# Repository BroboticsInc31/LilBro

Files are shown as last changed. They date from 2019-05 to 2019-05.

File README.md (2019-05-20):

# LilBro by Brobotics Inc. 

Lil'Bro is a 3D printed, open source quadrupedal robot which allows researchers to investigate agile gait locomotion and may duplicate, modify, and create new methods for the robot. 

Related Videos: </br>
Calibration - https://youtu.be/Aq8ONlaq-m4 </br>
Startup routine - https://youtu.be/N4R1693wzeQ </br>
Charging Batteries - https://youtu.be/PBRBTcRp_1k </br>
Using the power supply - https://youtu.be/rCxc9LMYpuw </br>

Install Dependencies: </br>
ODrive - https://docs.odriverobotics.com/ </br>
Numpy - https://www.numpy.org/</br></br>

Download the repository.</br>
in directory (where repository was downloaded) run:</br>
   ```
   sudo python3 main.py 
   ```
   </br>
   
</br></br>

broboticsinc

LilBro

Lil'Bro V1.0

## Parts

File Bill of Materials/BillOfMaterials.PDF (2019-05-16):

*NOTE:
- PRICES MAY VARY UPON CURRENT MARKET VALUE
- SHIPPINGNOT INCLUIDED; SHIPPING COST MAY VARY BASED ON DELIVERY LOCATION
APPROVAL DATE: | 1-29-2019
PART COUNT: | 512
TOTAL COST: | $2,187.77

Brobotics Inc. Purchased Bill of Materials
ITEM NO. | QTY. | PART NUMBER | DESCRIPTION | MATERIAL | VENDOR/NOTES | PRICE
1 | 12 | 509 | FASTENER, LEG MOUNT | PURCHASE | 93897A542 MCMASTER-CARR | $8.45 /25
2 | 12 | 510 | WASHER, LOCK | PURCHASE | 3573A16 MCMASTER-CARR | $8.21 /100
3 | 24 | 511 | NUT, HEX | PURCHASE | 96557A109 MCMASTER-CARR | $8.63 /50
4 | 4 | 512 | FASTENER, COVER | PURCHASE | 96817A274 MCMASTER-CARR | $6.69 /25
5 | 8 | 513 | MOTOR, DC | PURCHASE | D5065-270KV, ODRIVE | $69.00 EA
6 | 8 | 514 | ENCODER, CPR | PURCHASE | CVI AMT102-V, ODRIVE | $39.00 EA
7 | 16 | 515 | FASTENER, ENCODER | PURCHASE | 90666A104, MCMASTER-CARR | $8.40 /100
8 | 28 | 516 | HOLDER, CABLE | PURCHASE | 7565K31, MCMASTER-CARR | $5.74 /25
9 | 32 | 517 | FASTENER, MOTOR | PURCHASE | 93705A824, MCMASTER-CARR | $7.25 / 25
10 | 48 | 518 | FASTENER, MOTOR HOUSING | PURCHASE | 91292A114, MCMASTER-CARR | $4.72 /100
11 | 12 | 519 | LOCKNUT, LEG-JOINT | PURCHASE | 93795A205, MCMASTER-CARR | $10.94 /100
12 | 12 | 520 | FASTENER, LEG-JOINT | PURCHASE | 90278A375, MCMASTER-CARR | $3.79 EA
13 | 24 | 521 | BEARING, THRUST | PURCHASE | 6655K51, MCMASTER-CARR | $2.78 EA
14 | 24 | 522 | BEARING, SLEEVE | PURCHASE | 6679K33, MCMASTER-CARR | $2.31 EA
15 | 4 | 523 | FOOT, SLIP-ON | PURCHASE | 2517T71, MCMASTER-CARR | $6.64 /25
16 | 8 | 524 | HUB, MOTOR | PURCHASE | 2693, POLOLU | $6.99 /2
17 | 48 | 525 | FASTENER, HUB | PURCHASE | 92929A246, MCMASTER-CARR | $8.44 /100
18 | 26 | 526 | STANDOFF, HEX | PURCHASE | SPC-NLB3/KIT1-1, AMAZON | $9.99 /60
19 | 1 | 527 | COMPUTER, RASPBERRYPI | PURCHASE | 3775, ADAFRUIT INDUSTRIES | $35.00 EA
20 | 4 | 528 | DRIVER, MOTOR | PURCHASE | ODRIVE ROBOTICS | $129.00 EA
21 | 1 | 529 | BATTERY, DC | PURCHASE | 9067000373-0, HOBBY KING | $103.30 EA
22 | 34 38 4 | 531 532 530 | FASTENER, STANDOFF BRAKE RESISTOR NUT, STANDOFF | PURCHASE -- | 93840A126, MCMASTER-CARR INCLUDED W/ ITEM NO. 28 INCLUDED W/ ITEM NO. 26 | $5.55 /100 - 23 - 24
25 | 1 | 533 | INERTIAL MEASURE. UNIT | PURCHASE | GY-521MPU6050, AMAZON | $5.79 EA
26 | 1 | 534 | VOLTAGE REGULATOR | PURCHASE | SAINSMARTLM2596, AMAZON | $8.99 EA
27 | 36 | 535 | INSERT | PURCHASE | 94510A240, MCMASTER-CARR | $7.20 /50
28 | 1 | 536 | SWITCH, POWER | PURCHASE | UR198-2NO2NC, AMAZON | $10.78 EA
29 | 2 | 537 | HANDLE, CARRYING | PURCHASE | ASIN: B072XHBKPJ, AMAZON | $9.99 /2
30 | 4 | 538 | STRAP, BATTERY | PURCHASE | ASIN: B01MY2S7JD, AMAZON | $12.97 /10
31 | 12 | 539 | ZIP-TIES | PURCHASE | ASIN: B07C1HZD8T, AMAZON | $3.99 /100
32 | 9 | 540 | CONNECTORS, WIRE | PURCHASE | B07CWF8CRX, AMAZON | $13.99 /20
33 | 1 | 541 | CONTROLLER, PS3 | PURCHASE | ASIN: B07DQHY13L, AMAZON | $14.99 EA
34 | 4 | 542 | FILAMENT, 3D PRINTER | PURCHASE | MP05778, MAKERBOT | $42.99 EA
35 | 1 | 543 | WIRE, ELECTRICAL | PURCHASE | BNTECHGO10-18, AMAZON | $18.98 /30FT
36 | 8 | 544 | FAN, MOTOR COOLING | PURCHASE | NF-A4X10-FLX 5V, AMAZON | $13.95 EA
PURCHASED BILL OF
MATERIALS
SIZE A | DWG. NO. LB18-001 | REV
SCALE: 1:1 | WEIGHT: | SHEET 1 OF 1

TITLE:

A | A
B | B

2

2

1

1

ENG APPR. | FARRA, S
CHECKED | CARROLL, J
| NAME | SIGNATURE | DATE
COMPILED | RODRIGUEZ, E

SOLIDWORKS Educational Product. For Instructional Use Only.

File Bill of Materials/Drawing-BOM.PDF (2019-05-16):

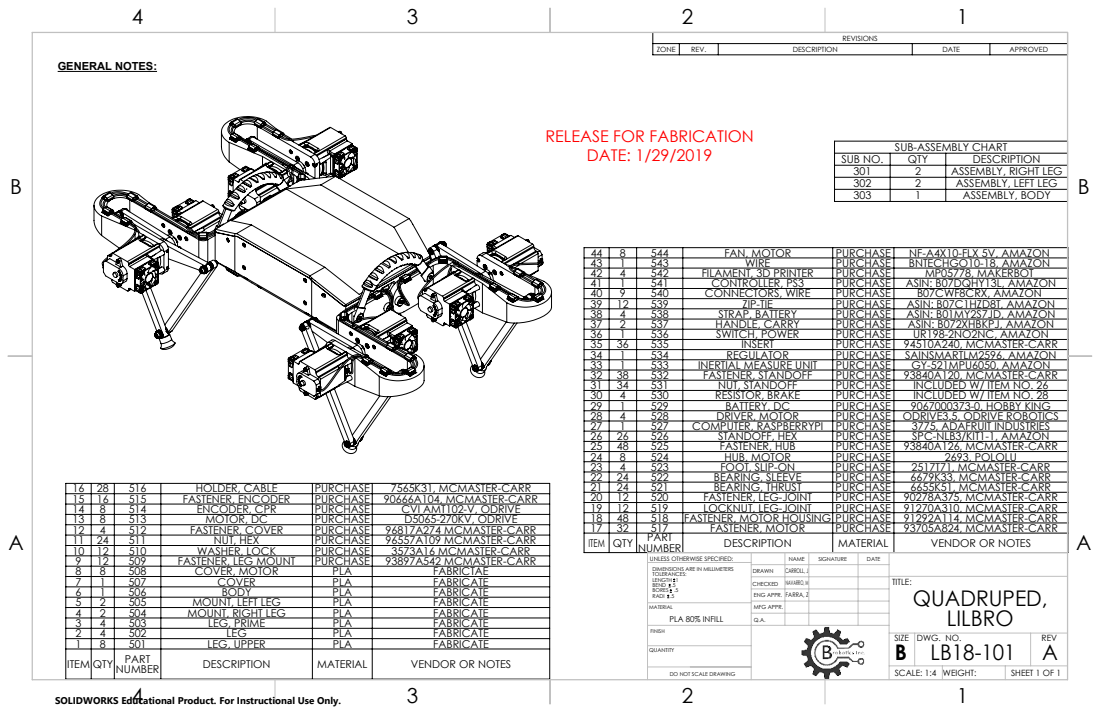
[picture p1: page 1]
GENERAL NOTES:; HOLDER, CABLE; PURCHASE; 7565K31, MCMASTER-CARR; FASTENER, ENCODER; 90666A104, MCMASTER-CARR; ENCODER, CPR; CVI AMT102-V, ODRIVE; MOTOR, DC; D5065-270KV, ODRIVE; FASTENER, COVER; 96817A274 MCMASTER-CARR; NUT, HEX; 96557A109 MCMASTER-CARR; BEARING, THRUST; 6655K51, MCMASTER-CARR; FASTENER, LEG-JOINT; 90278A375, MCMASTER-CARR; LOCKNUT, LEG-JOINT; 91270A310, MCMASTER-CARR; FASTENER, MOTOR HOUSING PURCHASE; 91292A114, MCMASTER-CARR; FASTENER, MOTOR; 93705A824, MCMASTER-CARR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

REVISIONS

ZONE | REV. | DESCRIPTION | DATE | APPROVED

RELEASE FOR FABRICATION
DATE: 1/29/2019

SUB-ASSEMBLY CHART

SUB NO. | QTY | DESCRIPTION
301 | 2 | ASSEMBLY, RIGHT LEG
302 | 2 | ASSEMBLY, LEFT LEG
303 | 1 | ASSEMBLY, BODY

44 | 8 | 544 | FAN, MOTOR | PURCHASE | NF-A4X10-FLX 5V, AMAZON
43 | 1 | 543 | WIRE | PURCHASE | BNTECHGO10-18, AMAZON
42 | 4 | 542 | FILAMENT, 3D PRINTER | PURCHASE | MP05778, MAKERBOT
41 | 1 | 541 | CONTROLLER, PS3 | PURCHASE | ASIN: B07DQHY13L, AMAZON
40 | 9 | 540 | CONNECTORS, WIRE | PURCHASE | B07CWF8CRX, AMAZON
39 | 12 | 539 | ZIP-TIE | PURCHASE | ASIN: B07C1HZD8T, AMAZON
38 | 4 | 538 | STRAP, BATTERY | PURCHASE | ASIN: B01MY2S7JD, AMAZON
37 | 2 | 537 | HANDLE, CARRY | PURCHASE | ASIN: B072XHBKPJ, AMAZON
36 | 1 | 536 | SWITCH, POWER | PURCHASE | UR198-2NO2NC, AMAZON
35 | 36 | 535 | INSERT | PURCHASE | 94510A240, MCMASTER-CARR
34 | 1 | 534 | REGULATOR | PURCHASE | SAINSMARTLM2596, AMAZON
33 | 1 | 533 | INERTIAL MEASURE UNIT | PURCHASE | GY-521MPU6050, AMAZON
32 | 38 | 532 | FASTENER, STANDOFF | PURCHASE | 93840A120, MCMASTER-CARR
31 | 34 | 531 | NUT, STANDOFF | PURCHASE | INCLUDED W/ ITEM NO. 26
30 | 4 | 530 | RESISTOR, BRAKE | PURCHASE | INCLUDED W/ ITEM NO. 28
29 | 1 | 529 | BATTERY, DC | PURCHASE | 9067000373-0, HOBBY KING
28 | 4 | 528 | DRIVER, MOTOR | PURCHASE | ODRIVE3.5, ODRIVE ROBOTICS
27 | 1 | 527 | COMPUTER, RASPBERRYPI | PURCHASE | 3775, ADAFRUIT INDUSTRIES
26 | 26 | 526 | STANDOFF, HEX | PURCHASE | SPC-NLB3/KIT1-1, AMAZON
25 | 48 | 525 | FASTENER, HUB | PURCHASE | 93840A126, MCMASTER-CARR
24 | 8 | 524 | HUB, MOTOR | PURCHASE | 2693, POLOLU
23 | 4 | 523 | FOOT, SLIP-ON | PURCHASE | 2517T71, MCMASTER-CARR
22 | 24 | 522 | BEARING, SLEEVE | PURCHASE | 6679K33, MCMASTER-CARR

10 | 12 | 510 | WASHER, LOCK | PURCHASE | 3573A16 MCMASTER-CARR
9 | 12 | 509 | FASTENER, LEG MOUNT | PURCHASE | 93897A542 MCMASTER-CARR
8 | 8 | 508 | COVER, MOTOR | PLA | FABRICTAE | DIMENSIONS ARE IN MILLIMETERS TOLERANCES: LENGTH 1 BEND .5 BORES .5 RADI .5 | DRAWN | CARROLL, J
7 | 1 | 507 | COVER | PLA | FABRICATE | | CHECKED | NAVARRO, M | TITLE: QUADRUPED, LILBRO
6 | 1 | 506 | BODY | PLA | FABRICATE | | ENG APPR. | FARRA, Z
5 | 2 | 505 | MOUNT, LEFT LEG | PLA | FABRICATE
4 | 2 | 504 | MOUNT, RIGHT LEG | PLA | FABRICATE
3 | 4 | 503 | LEG, PRIME | PLA | FABRICATE
2 | 4 | 502 | LEG | PLA | FABRICATE
1 | 8 | 501 | LEG, UPPER | PLA | FABRICATE
ITEM QTY | | PART NUMBER | DESCRIPTION | MATERIAL | VENDOR OR NOTES

UNLESS OTHERWISE SPECIFIED: | NAME | SIGNATURE | DATE

MATERIAL PLA 80% INFILL | MFG APPR.

FINISH

SIZE B | DWG. NO. LB18-101 | REV A

DO NOT SCALE DRAWING | | SCALE: 1:4 | WEIGHT: | SHEET 1 OF 1

SOLIDWORKS Educational Product. For Instructional Use Only.

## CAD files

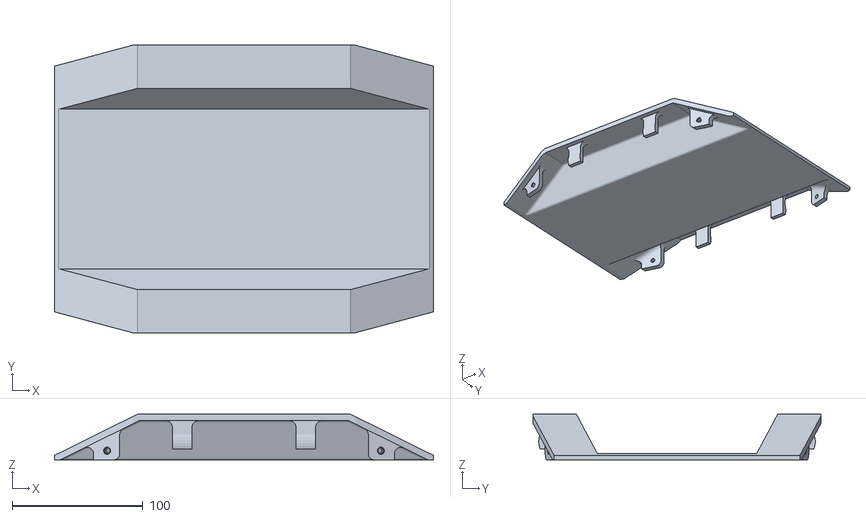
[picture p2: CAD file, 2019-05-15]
STL_Files/Body/Part 507 Cover (New).STL
290.0 x 220.0 x 35.0

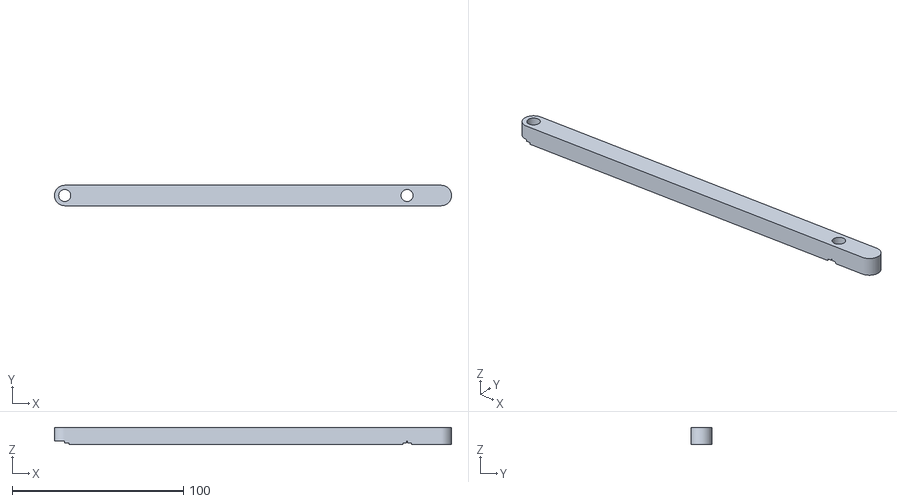
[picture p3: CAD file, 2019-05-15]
STL_Files/Legs/503 Leg, Prime (Version 1.2 Updated Jan 2019).STL
232.0 x 12.0 x 10.0

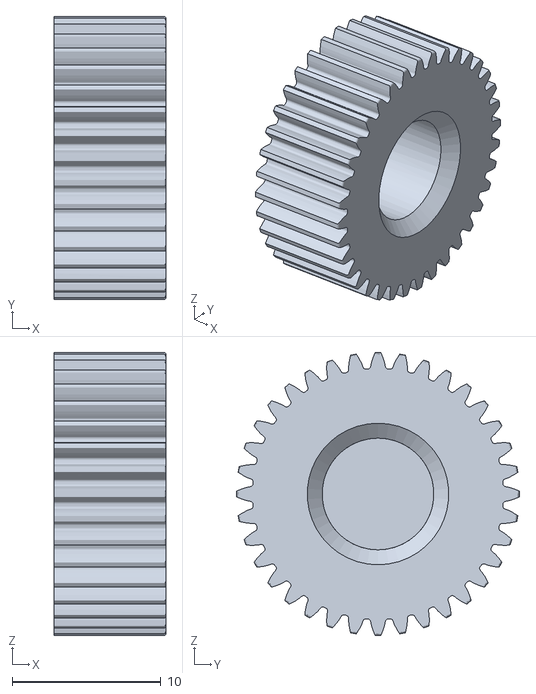
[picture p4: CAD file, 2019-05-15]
STL_Files/Legs/GearBox/Planet.STL
7.50 x 19.0 x 19.0

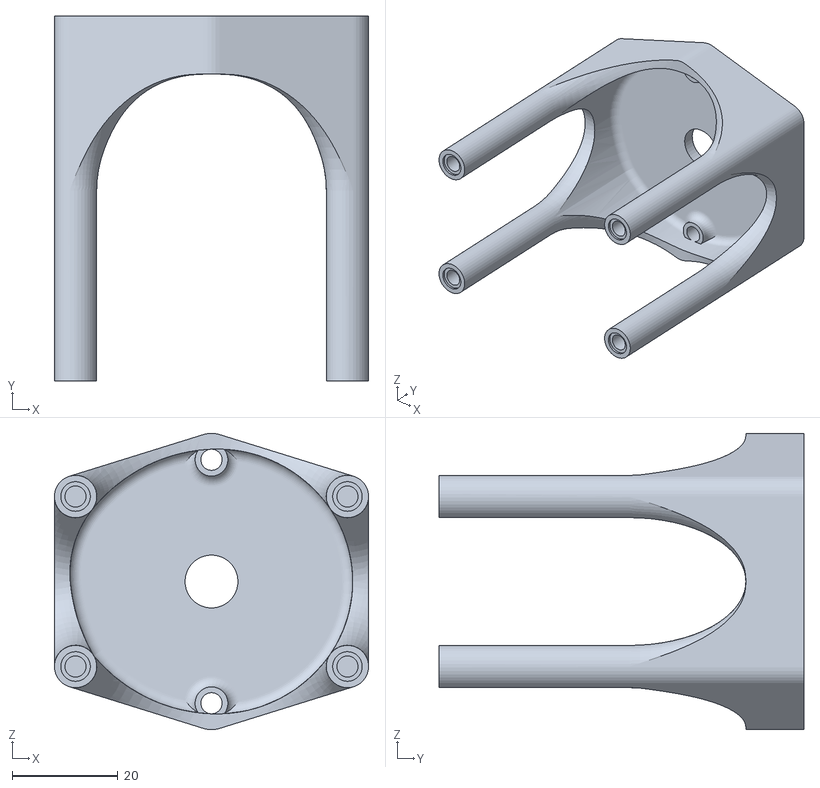
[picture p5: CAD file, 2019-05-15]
STL_Files/Mounts/Part 508 Cover, Motor (New).STL
59.4 x 69.0 x 56.0

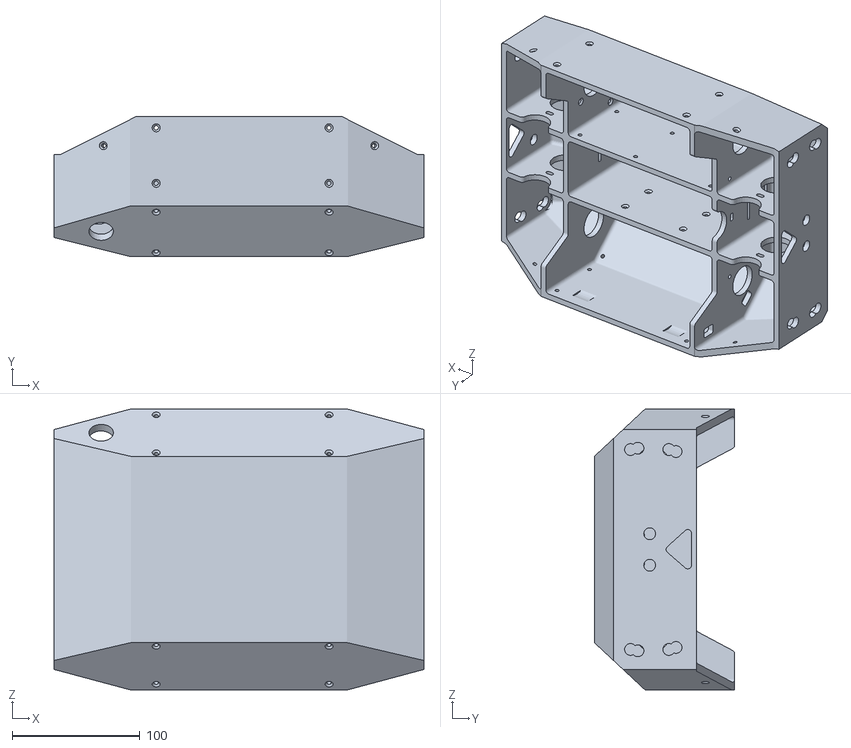
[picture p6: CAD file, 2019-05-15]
STL_Files/Body/Part 506 Body.STL
290.0 x 110.0 x 220.0

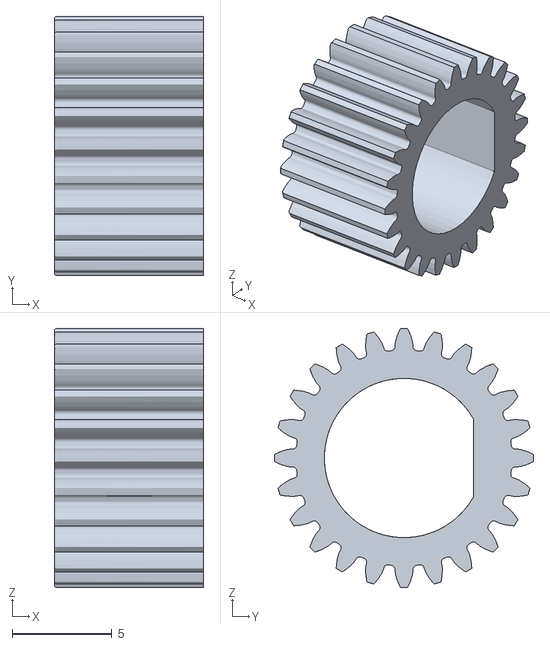
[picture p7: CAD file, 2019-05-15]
STL_Files/Legs/GearBox/Sun.STL
7.50 x 13.0 x 13.0

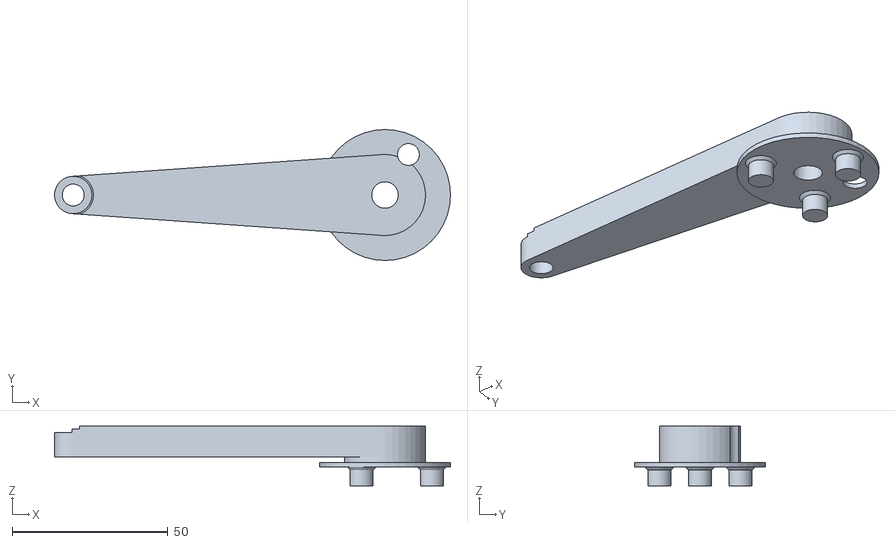
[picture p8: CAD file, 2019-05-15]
STL_Files/Legs/Upper leg.STL
127.0 x 42.0 x 19.2

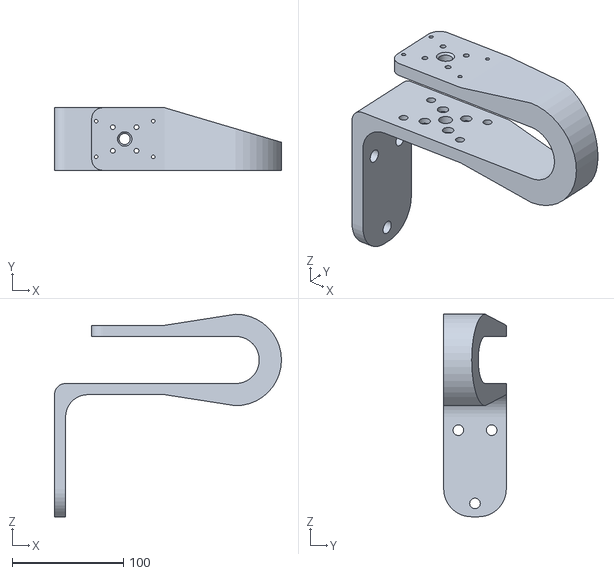
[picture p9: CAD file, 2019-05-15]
STL_Files/Mounts/505 Mount, Left Leg (Version 1.3 Updated Jan 2019).STL
204.4 x 56.4 x 182.4

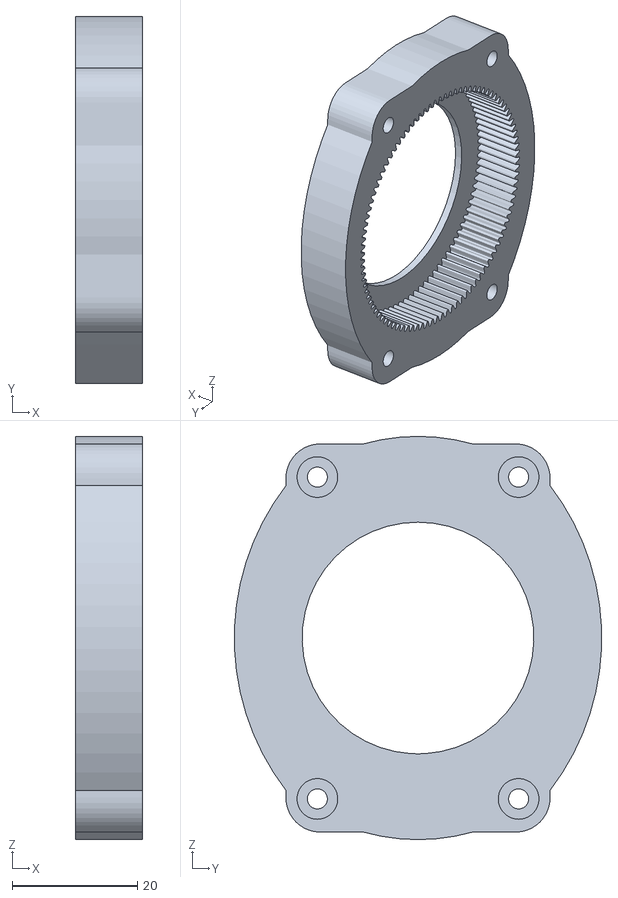
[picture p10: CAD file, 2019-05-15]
STL_Files/Legs/GearBox/Ring.STL
10.8 x 58.6 x 64.4

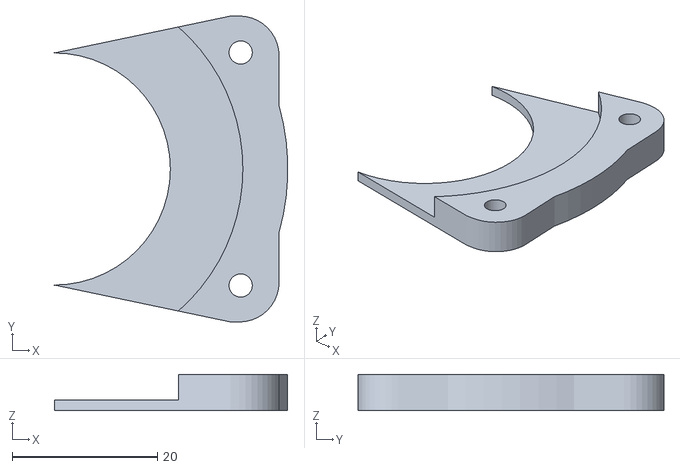
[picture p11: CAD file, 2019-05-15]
STL_Files/Legs/GearBox/Cap.STL
32.2 x 42.2 x 5.00

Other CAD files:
STL_Files/Mounts/504 Mount, Right Leg (Version 1.3 Updated Jan 2019).STL

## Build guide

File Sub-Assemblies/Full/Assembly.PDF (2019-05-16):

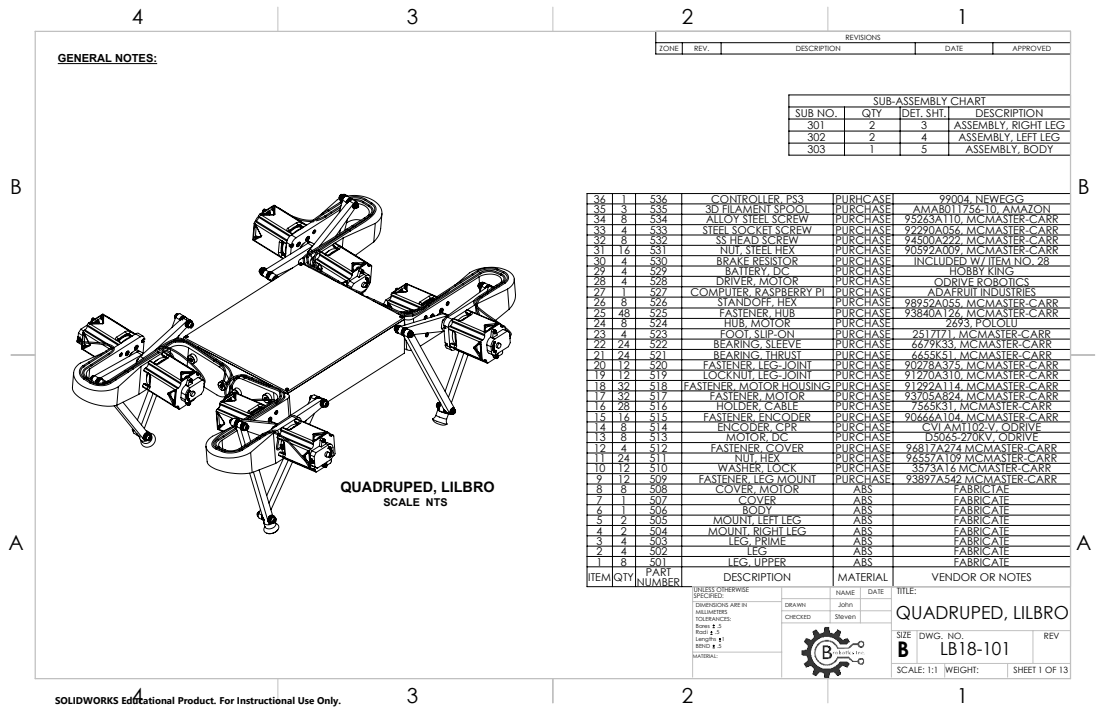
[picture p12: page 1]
GENERAL NOTES:; QUADRUPED, LILBRO SCALE NTS; DIMENSIONS ARE IN; Bores .5 Radi .5 Lengths 1 BEND .5

REVISIONS

ZONE | REV. | DESCRIPTION | DATE | APPROVED

SUB-ASSEMBLY CHART

SUB NO. | QTY | DET. SHT. | DESCRIPTION
301 | 2 | 3 | ASSEMBLY, RIGHT LEG
302 | 2 | 4 | ASSEMBLY, LEFT LEG
303 | 1 | 5 | ASSEMBLY, BODY

36 | 1 | 536 | CONTROLLER, PS3 | PURHCASE | 99004, NEWEGG
35 | 3 | 535 | 3D FILAMENT SPOOL | PURCHASE | AMAB011756-10, AMAZON
34 | 8 | 534 | ALLOY STEEL SCREW | PURCHASE | 95263A110, MCMASTER-CARR
33 | 4 | 533 | STEEL SOCKET SCREW | PURCHASE | 92290A056, MCMASTER-CARR
32 | 8 | 532 | SS HEAD SCREW | PURCHASE | 94500A222, MCMASTER-CARR
31 | 16 | 531 | NUT, STEEL HEX | PURCHASE | 90592A009, MCMASTER-CARR
30 | 4 | 530 | BRAKE RESISTOR | PURCHASE | INCLUDED W/ ITEM NO. 28
29 | 4 | 529 | BATTERY, DC | PURCHASE | HOBBY KING
28 | 4 | 528 | DRIVER, MOTOR | PURCHASE | ODRIVE ROBOTICS
27 | 1 | 527 | COMPUTER, RASPBERRY PI | PURCHASE | ADAFRUIT INDUSTRIES
26 | 8 | 526 | STANDOFF, HEX | PURCHASE | 98952A055, MCMASTER-CARR
25 | 48 | 525 | FASTENER, HUB | PURCHASE | 93840A126, MCMASTER-CARR
24 | 8 | 524 | HUB, MOTOR | PURCHASE | 2693, POLOLU
23 | 4 | 523 | FOOT, SLIP-ON | PURCHASE | 2517T71, MCMASTER-CARR
22 | 24 | 522 | BEARING, SLEEVE | PURCHASE | 6679K33, MCMASTER-CARR
21 | 24 | 521 | BEARING, THRUST | PURCHASE | 6655K51, MCMASTER-CARR
20 | 12 | 520 | FASTENER, LEG-JOINT | PURCHASE | 90278A375, MCMASTER-CARR
19 | 12 | 519 | LOCKNUT, LEG-JOINT | PURCHASE | 91270A310, MCMASTER-CARR
18 | 32 | 518 | FASTENER, MOTOR HOUSING | PURCHASE | 91292A114, MCMASTER-CARR
17 | 32 | 517 | FASTENER, MOTOR | PURCHASE | 93705A824, MCMASTER-CARR
16 | 28 | 516 | HOLDER, CABLE | PURCHASE | 7565K31, MCMASTER-CARR
15 | 16 | 515 | FASTENER, ENCODER | PURCHASE | 90666A104, MCMASTER-CARR
14 | 8 | 514 | ENCODER, CPR | PURCHASE | CVI AMT102-V, ODRIVE
13 | 8 | 513 | MOTOR, DC | PURCHASE | D5065-270KV, ODRIVE
12 | 4 | 512 | FASTENER, COVER | PURCHASE | 96817A274 MCMASTER-CARR
11 | 24 | 511 | NUT, HEX | PURCHASE | 96557A109 MCMASTER-CARR
10 | 12 | 510 | WASHER, LOCK | PURCHASE | 3573A16 MCMASTER-CARR
9 | 12 | 509 | FASTENER, LEG MOUNT | PURCHASE | 93897A542 MCMASTER-CARR
8 | 8 | 508 | COVER, MOTOR | ABS | FABRICTAE
7 | 1 | 507 | COVER | ABS | FABRICATE
6 | 1 | 506 | BODY | ABS | FABRICATE
5 | 2 | 505 | MOUNT, LEFT LEG | ABS | FABRICATE
4 | 2 | 504 | MOUNT, RIGHT LEG | ABS | FABRICATE
3 | 4 | 503 | LEG, PRIME | ABS | FABRICATE
2 | 4 | 502 | LEG | ABS | FABRICATE
1 | 8 | 501 | LEG, UPPER | ABS | FABRICATE
ITEM QTY | | PART NUMBER | DESCRIPTION | MATERIAL | VENDOR OR NOTES

SPECIFIED: | | NAME UNLESS OTHERWISE | DATE | TITLE: QUADRUPED, LILBRO

DRAWN | Steven John
CHECKED

SIZE B | DWG. NO. LB18-101 | REV

SCALE: 1:1 | WEIGHT: | SHEET 1 OF 13

SOLIDWORKS Educational Product. For Instructional Use Only.

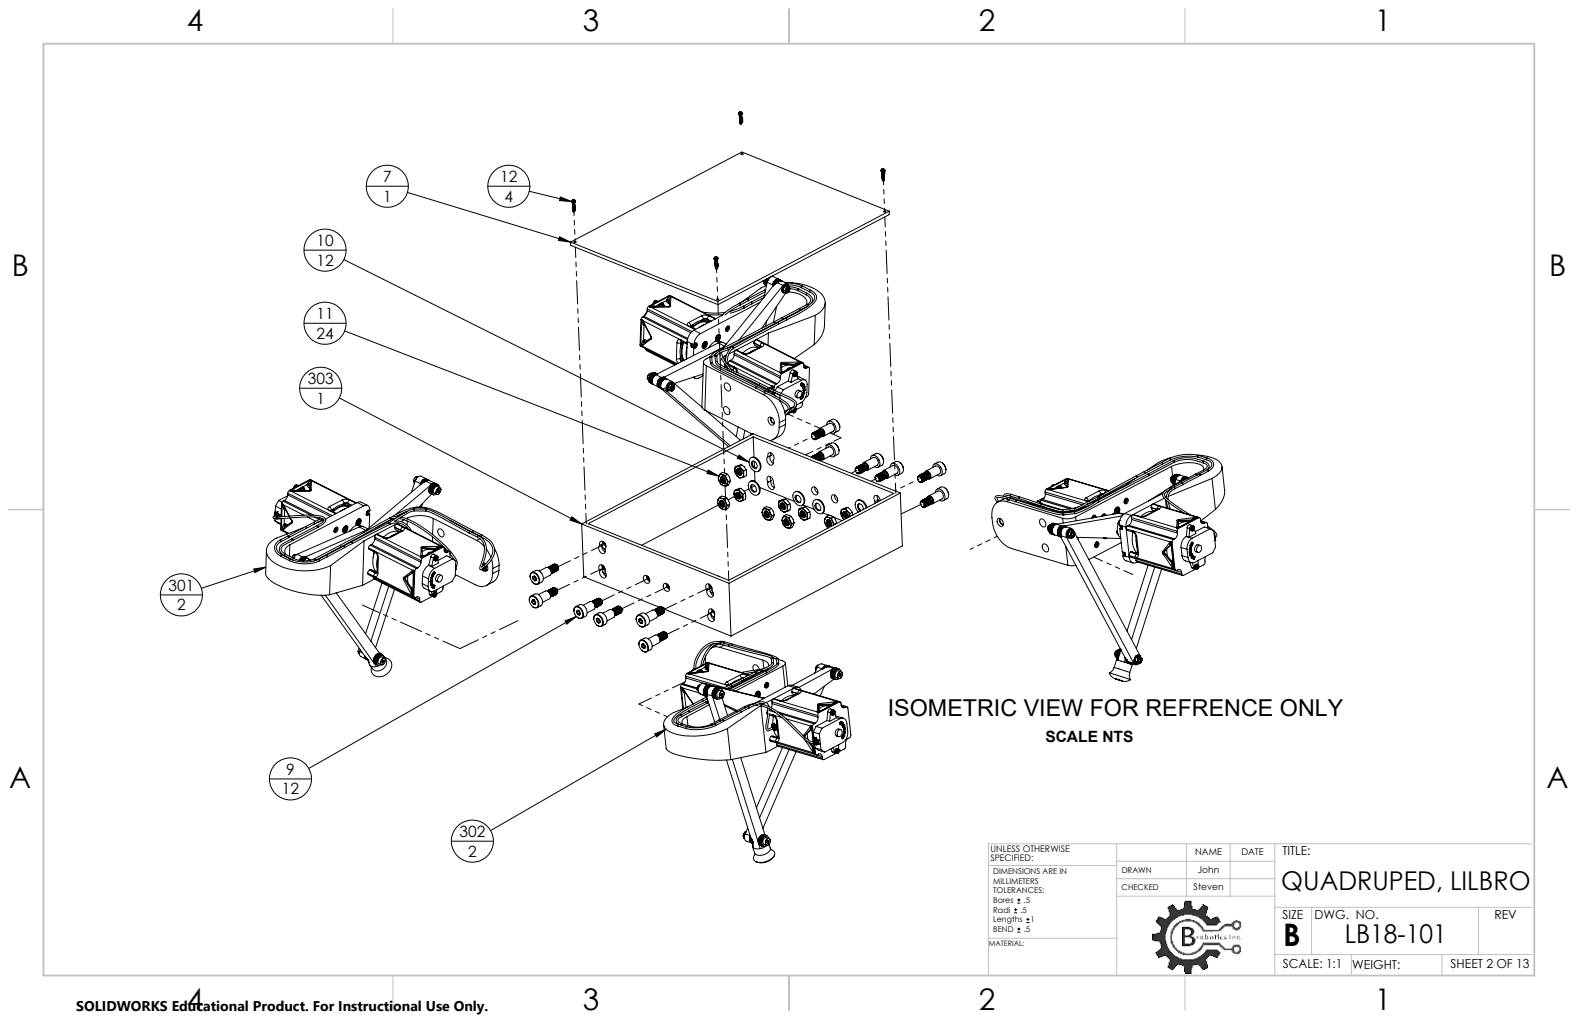
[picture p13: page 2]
SCALE NTS; DIMENSIONS ARE IN; Bores .5 Radi .5 Lengths 1 BEND .5

ISOMETRIC VIEW FOR REFRENCE ONLY

SPECIFIED: | | NAME UNLESS OTHERWISE | DATE | TITLE: QUADRUPED, LILBRO

DRAWN | Steven John
CHECKED

SIZE B | DWG. NO. LB18-101 | REV

SCALE: 1:1 | WEIGHT:

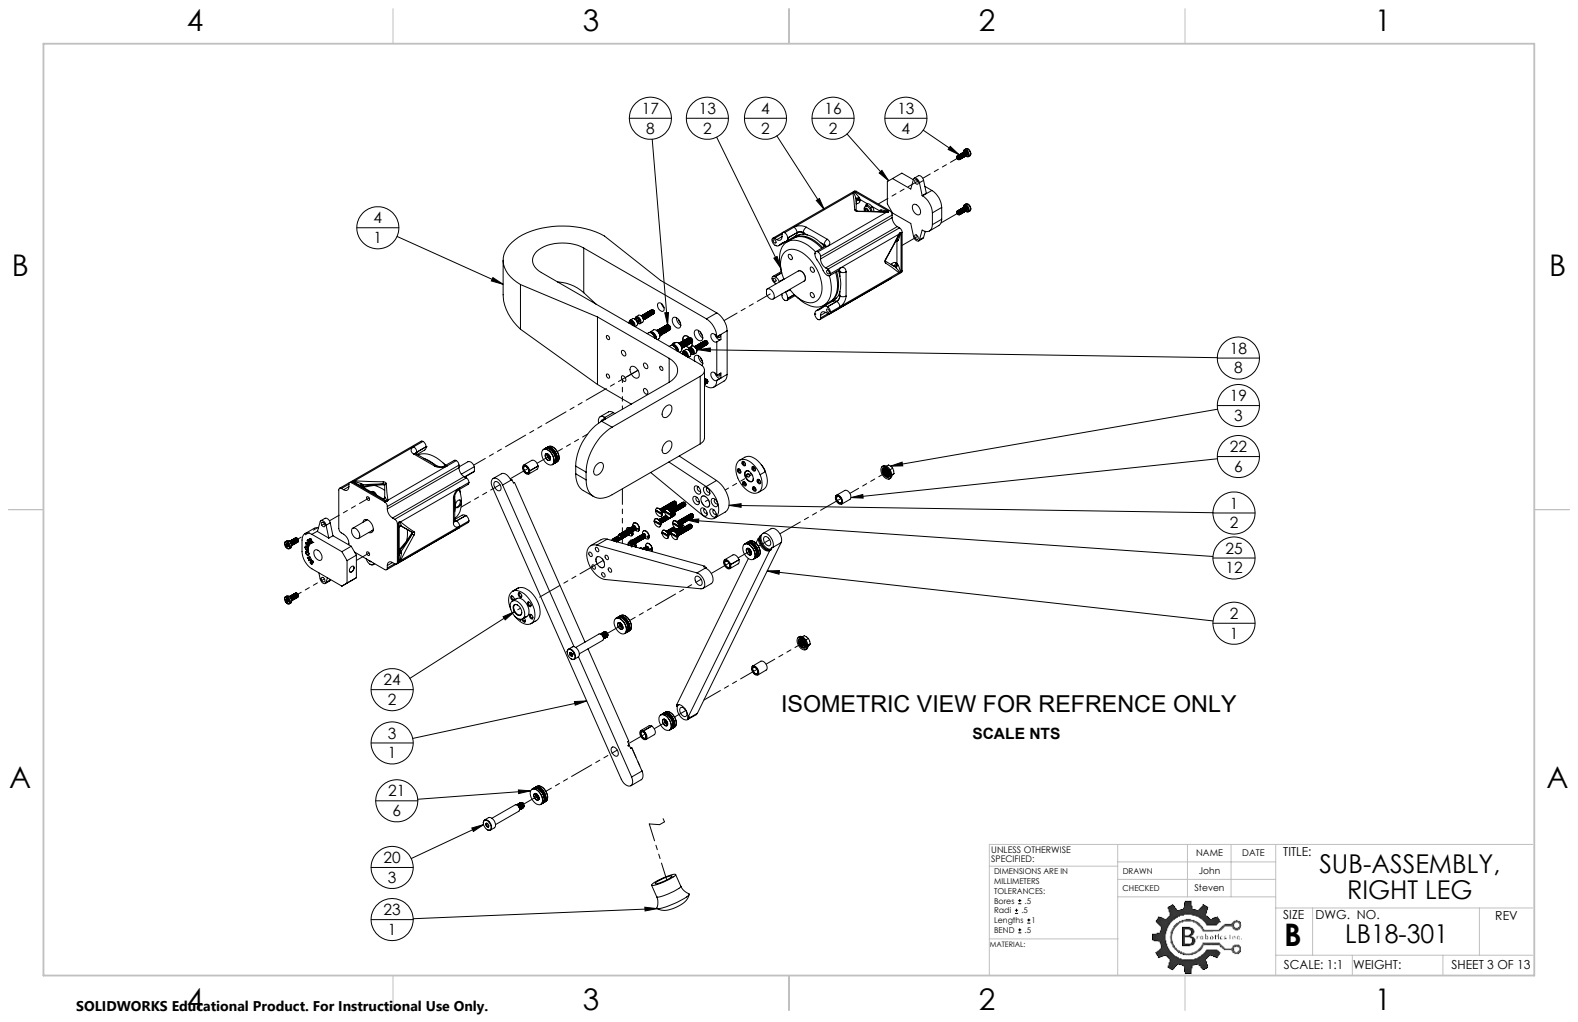
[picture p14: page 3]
SCALE NTS; DIMENSIONS ARE IN; Bores .5 Radi .5 Lengths 1 BEND .5

ISOMETRIC VIEW FOR REFRENCE ONLY

SPECIFIED: | | NAME UNLESS OTHERWISE | DATE | TITLE: SUB-ASSEMBLY, RIGHT LEG

DRAWN | John
CHECKED | Steven

SIZE B | DWG. NO. LB18-301 | REV

SCALE: 1:1 | WEIGHT:

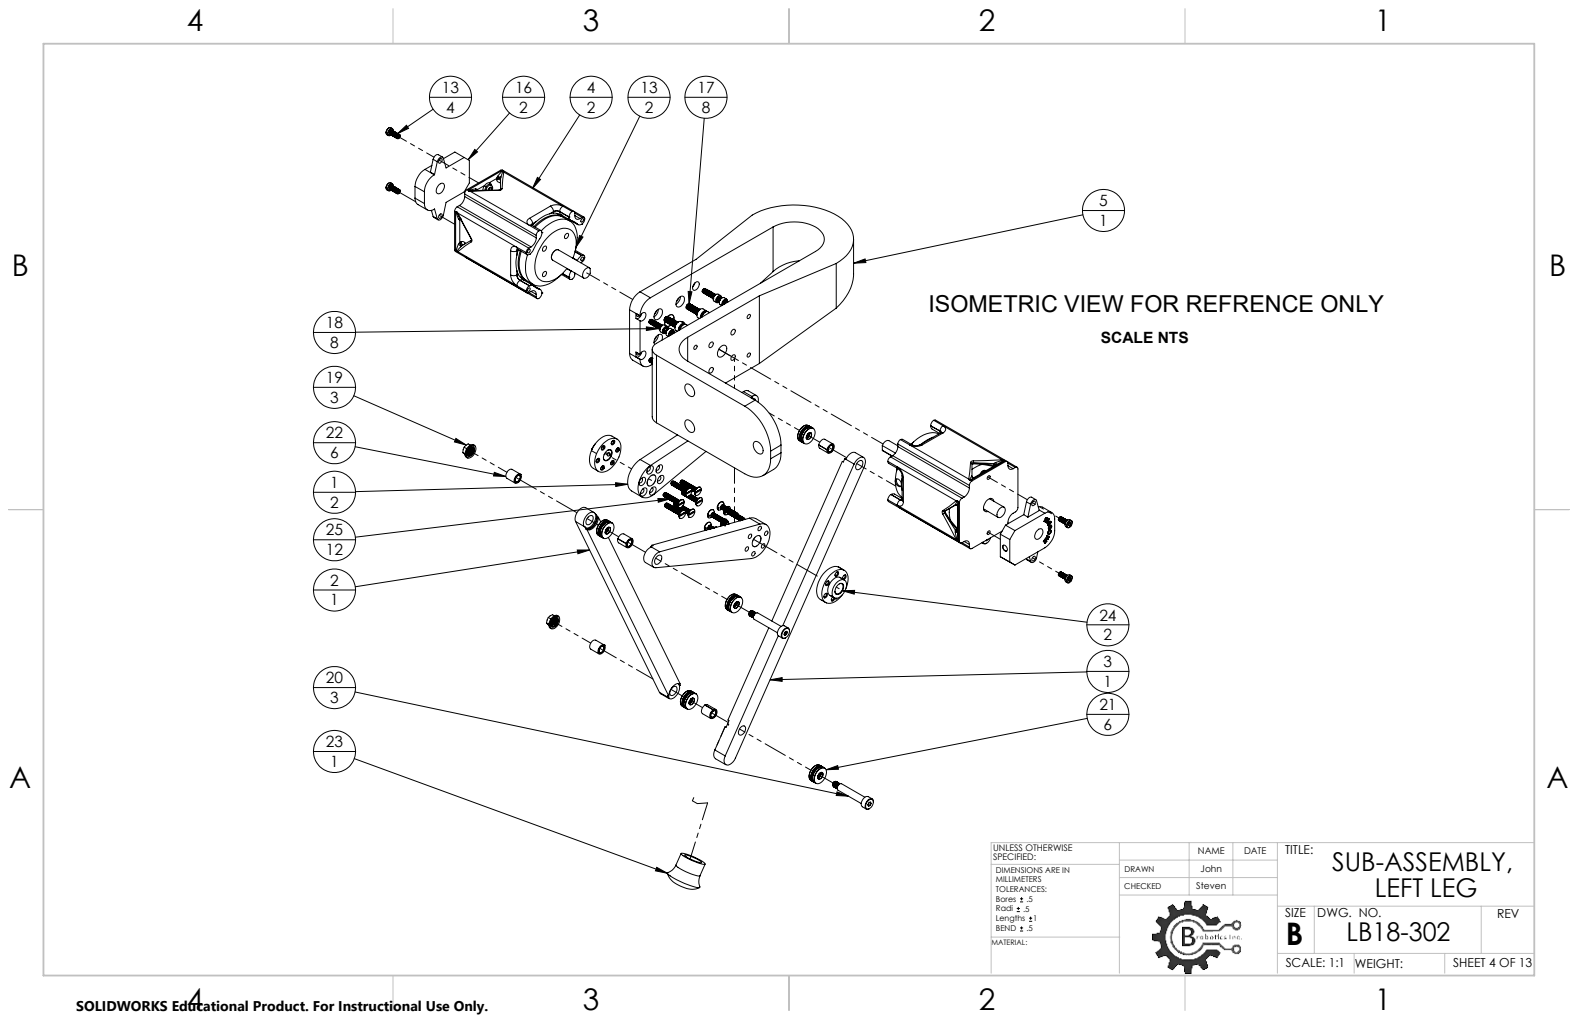
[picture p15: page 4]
SCALE NTS; DIMENSIONS ARE IN; Bores .5 Radi .5 Lengths 1 BEND .5

ISOMETRIC VIEW FOR REFRENCE ONLY

SPECIFIED: | | NAME UNLESS OTHERWISE | DATE | TITLE: SUB-ASSEMBLY, LEFT LEG

DRAWN | John
CHECKED | Steven

SIZE B | DWG. NO. LB18-302 | REV

SCALE: 1:1 | WEIGHT:

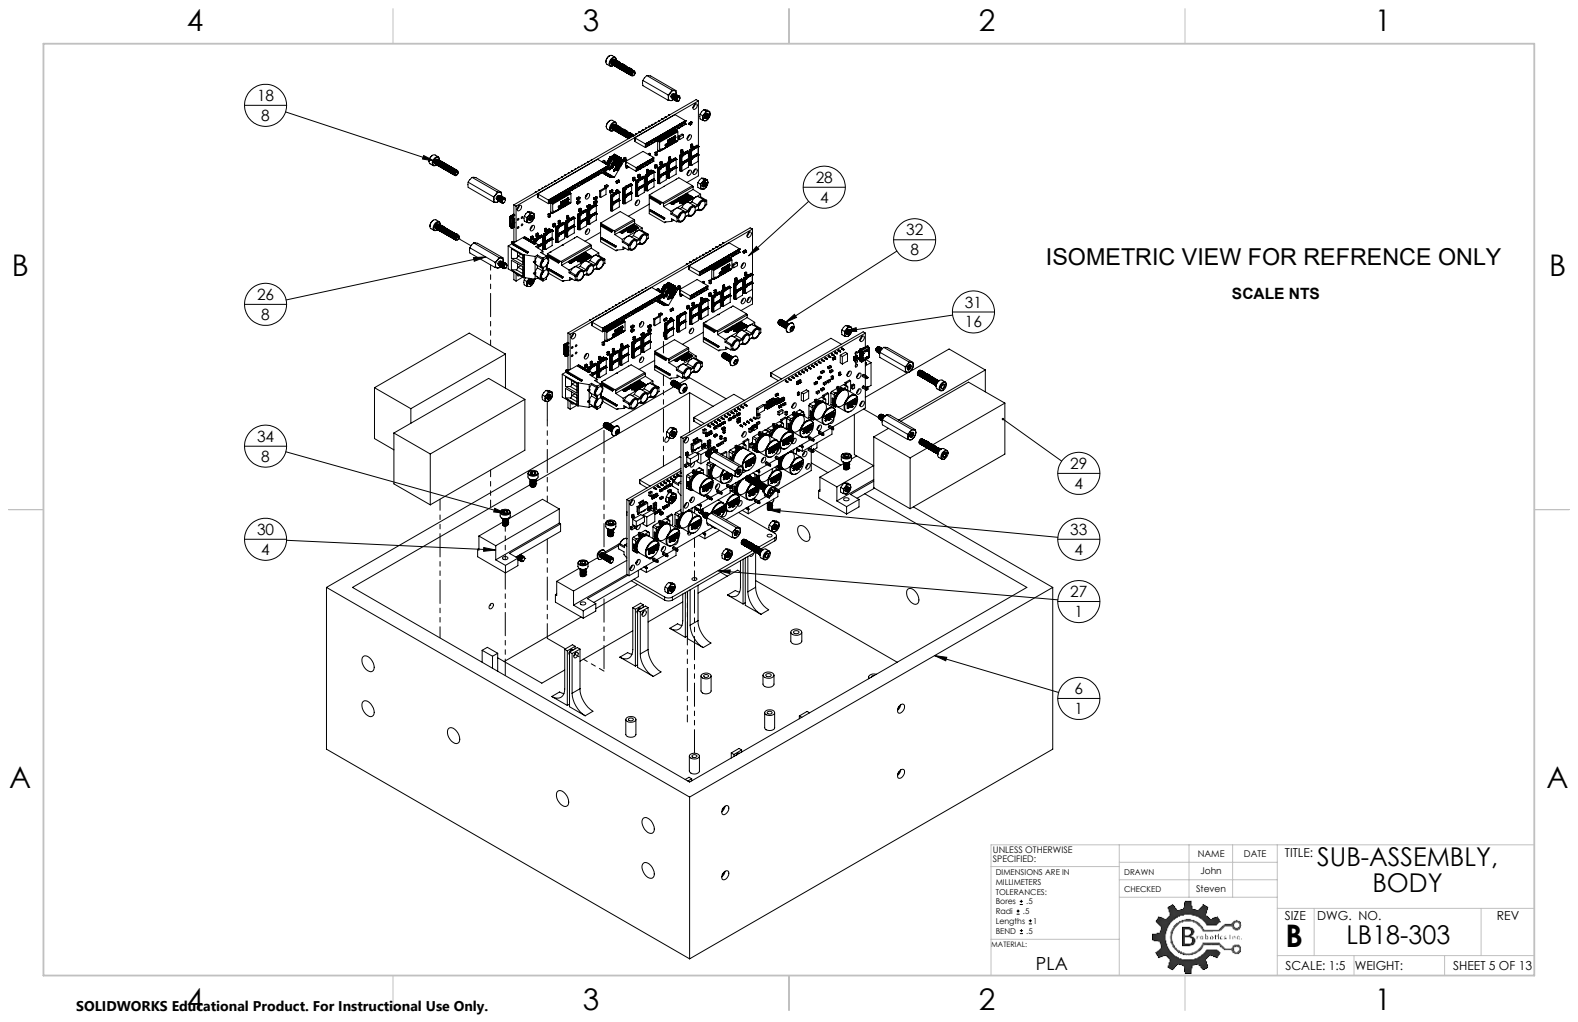
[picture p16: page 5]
ISOMETRIC VIEW FOR REFRENCE ONLY; SCALE NTS; DIMENSIONS ARE IN; Bores .5 Radi .5 Lengths 1 BEND .5

UNLESS OTHERWISE SPECIFIED: | | NAME | DATE | SUB-ASSEMBLY, TITLE: BODY

DRAWN | Steven John
CHECKED

SIZE B | DWG. NO. LB18-303 | REV

SCALE: 1:5 | WEIGHT:

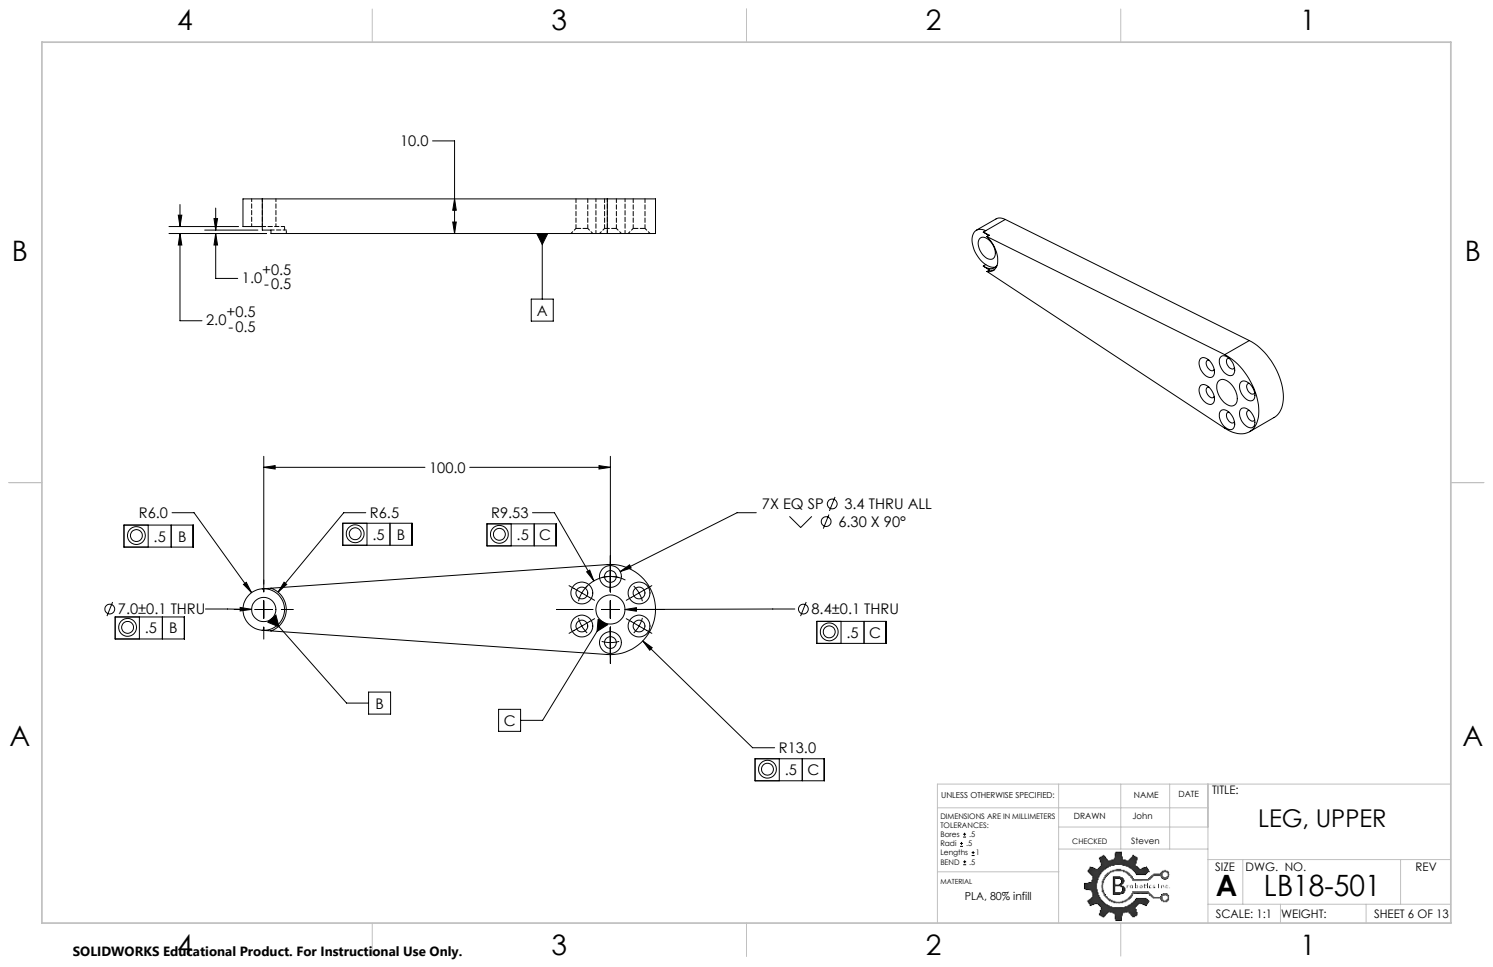
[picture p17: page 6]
7.0±0.1 THRU; 8.4±0.1 THRU; 7X EQ SP 3.4 THRU ALL; PLA, 80% infill

UNLESS OTHERWISE SPECIFIED: | | NAME | DATE | TITLE: LEG, UPPER

DIMENSIONS ARE IN MILLIMETERS TOLERANCES: Bores .5 Radi .5 Lengths 1 BEND .5 | DRAWN | John

CHECKED | Steven

SIZE A | DWG. NO. LB18-501 | REV

SCALE: 1:1 | WEIGHT: | SHEET 6 OF 13

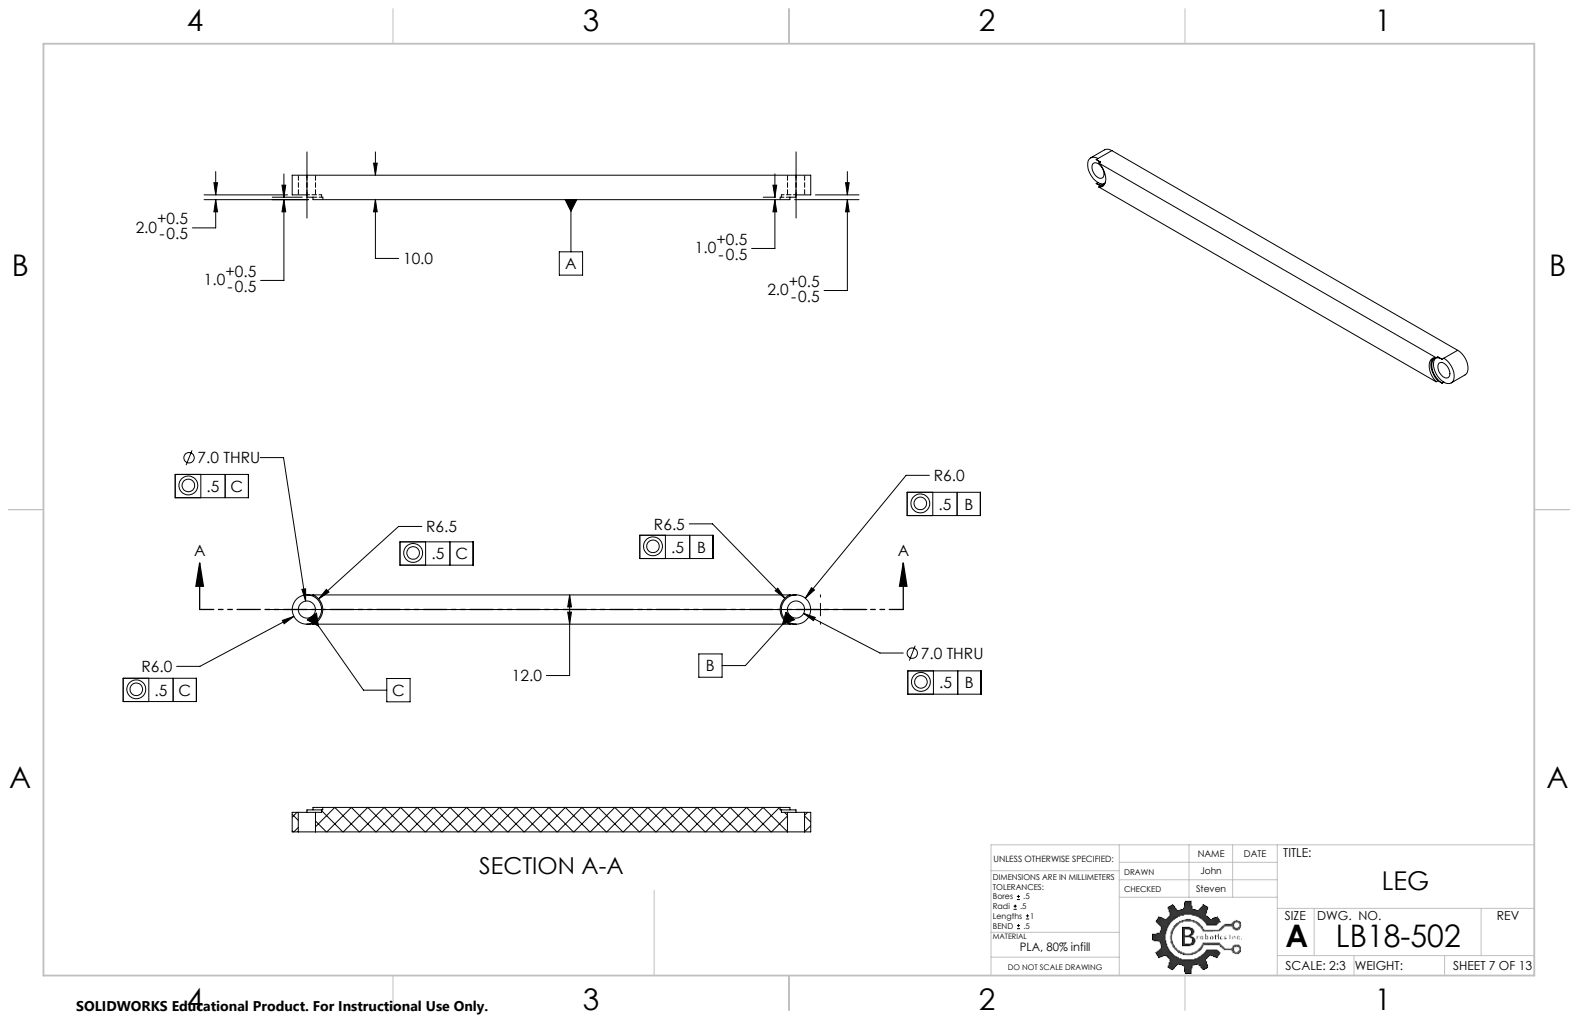
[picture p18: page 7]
7.0 THRU; SECTION A-A

NAME UNLESS OTHERWISE SPECIFIED: | DATE | TITLE: LEG

DIMENSIONS ARE IN MILLIMETERS
TOLERANCES:
Bores .5
Radi .5
Lengths 1
BEND .5
MATERIAL
PLA, 80% infill

DRAWN | John
CHECKED | Steven

SIZE A | DWG. NO. LB18-502 | REV

DO NOT SCALE DRAWING | | SCALE: 2:3 | WEIGHT:

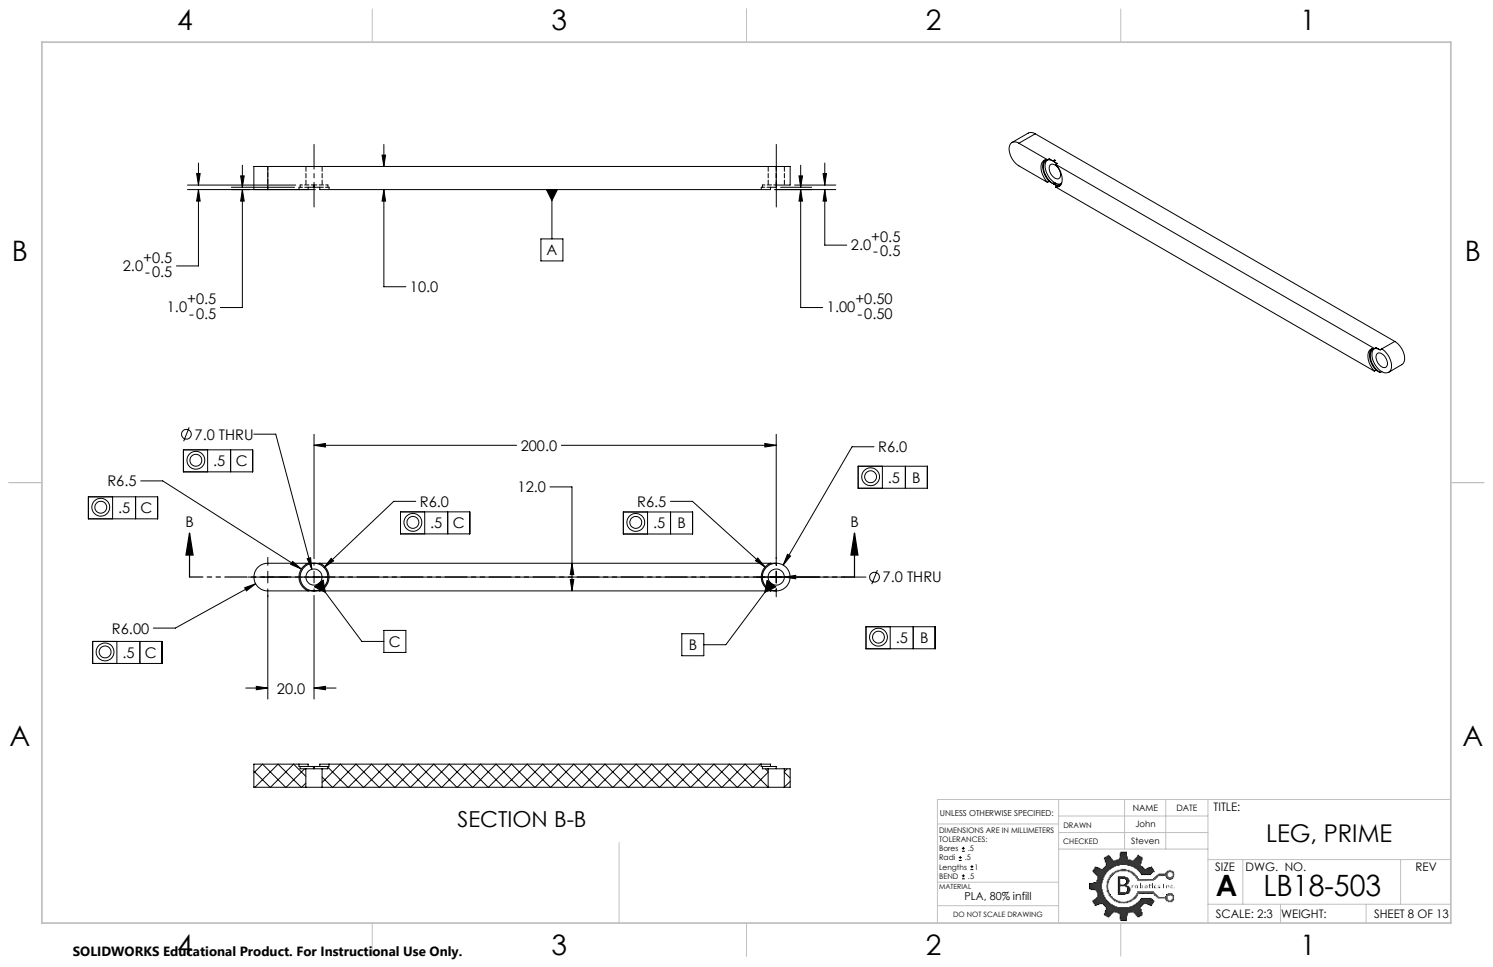
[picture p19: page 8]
7.0 THRU; SECTION B-B

NAME UNLESS OTHERWISE SPECIFIED: | DATE | TITLE: LEG, PRIME

DIMENSIONS ARE IN MILLIMETERS
TOLERANCES:
Bores .5
Radi .5
Lengths 1
BEND .5
MATERIAL
PLA, 80% infill

DRAWN | John
CHECKED | Steven

SIZE A | DWG. NO. LB18-503 | REV

DO NOT SCALE DRAWING | | SCALE: 2:3 | WEIGHT:

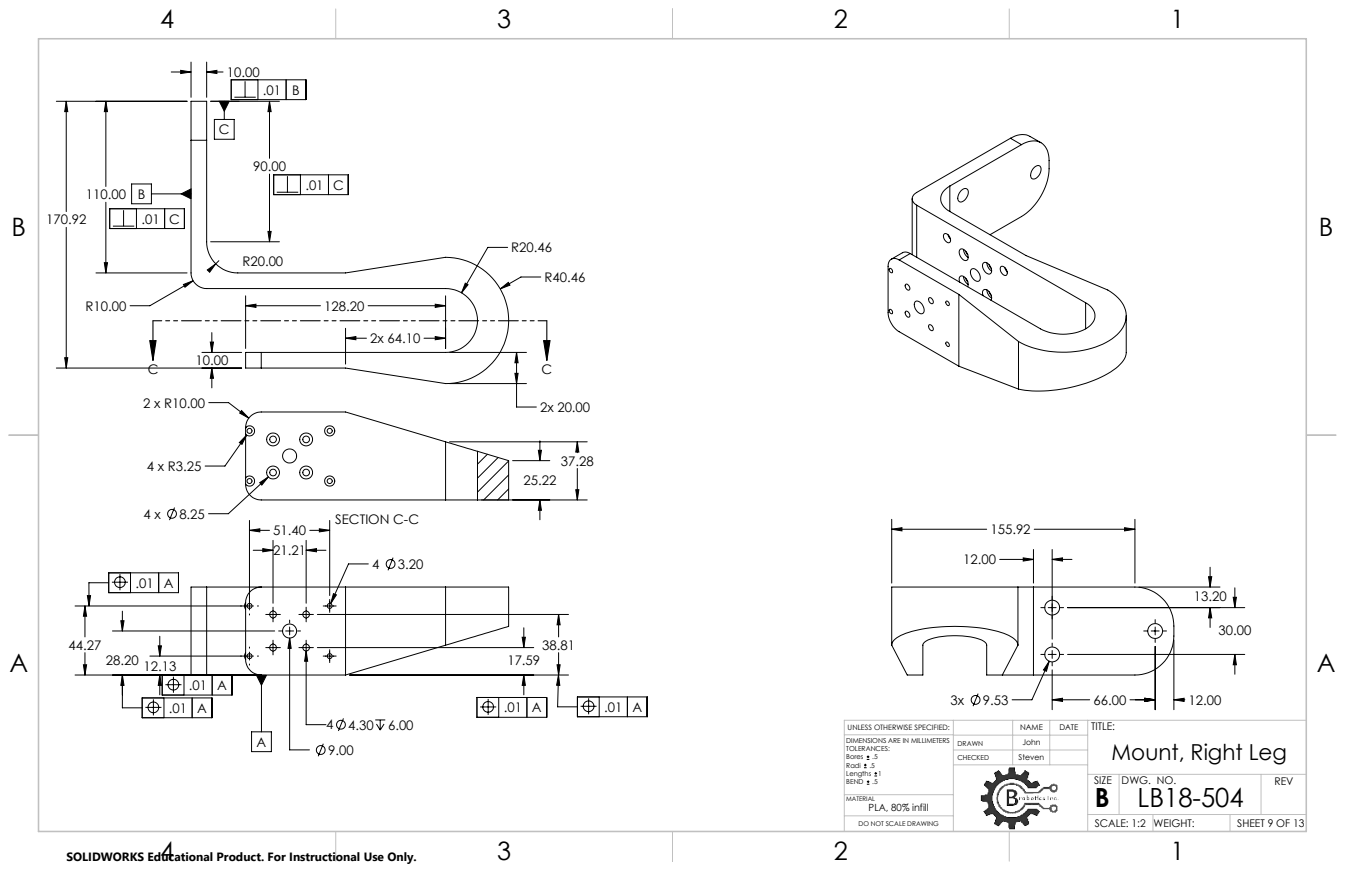
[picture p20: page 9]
SECTION C-C; PLA, 80% infill

UNLESS OTHERWISE SPECIFIED: | | NAME | DATE | TITLE: Mount, Right Leg
DIMENSIONS ARE IN MILLIMETERS TOLERANCES: Bores .5 Radi .5 Lengths 1 BEND .5 | DRAWN | John

CHECKED | Steven

SIZE B | DWG. NO. LB18-504 | REV

DO NOT SCALE DRAWING | | SCALE: 1:2 | WEIGHT:

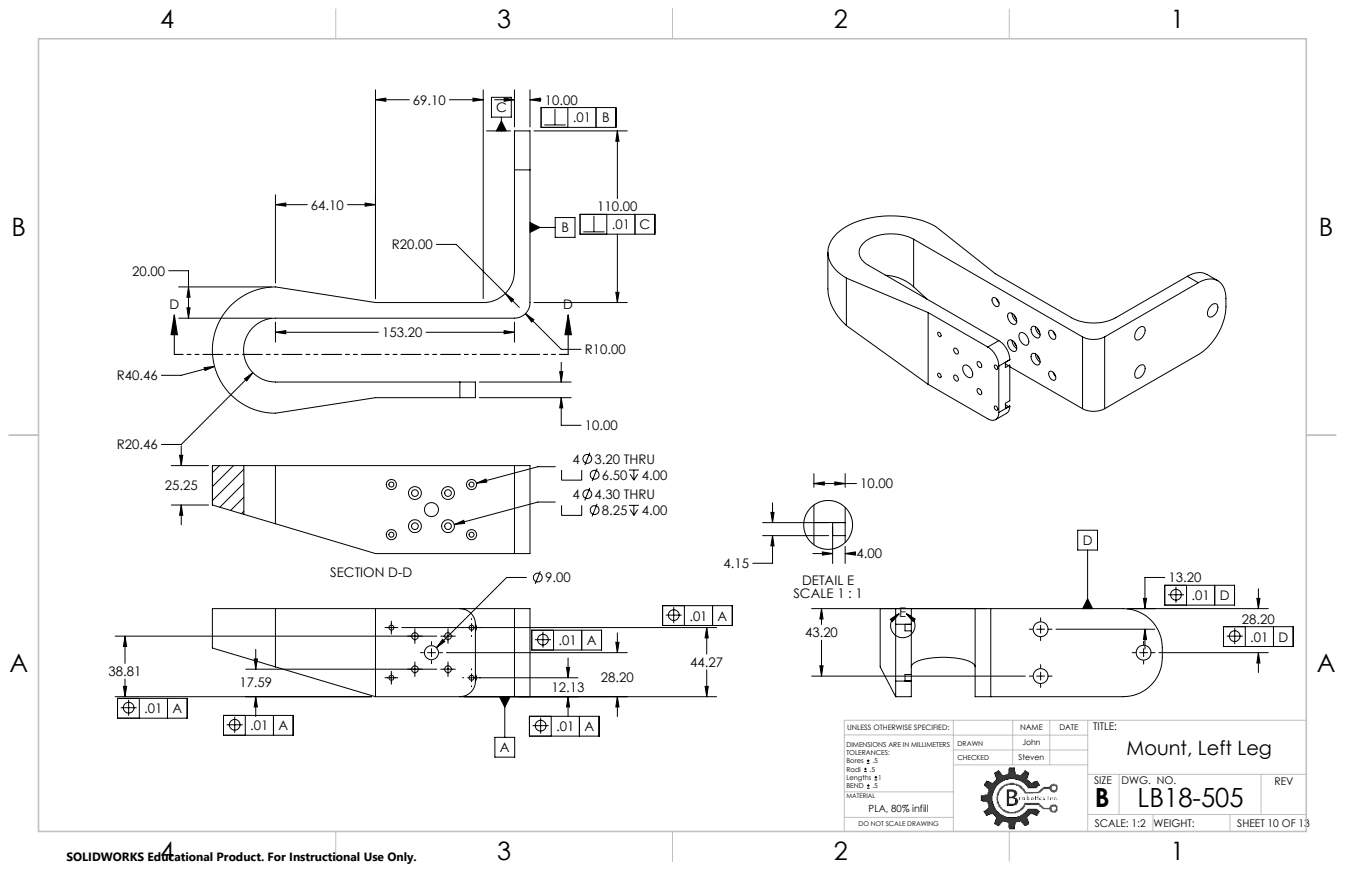
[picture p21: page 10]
4 3.20 THRU 6.50 4.00 4 4.30 THRU 8.25 4.00; SECTION D-D; 4.00 4.15 DETAIL E SCALE 1 : 1

UNLESS OTHERWISE SPECIFIED: | NAME | DATE | TITLE: Mount, Left Leg

DIMENSIONS ARE IN MILLIMETERS
TOLERANCES:
Bores .5
Radi .5
Lengths 1
BEND .5
MATERIAL
PLA, 80% infill

SIZE B | DWG. NO. LB18-505 | REV

DO NOT SCALE DRAWING | | SCALE: 1:2 | WEIGHT:

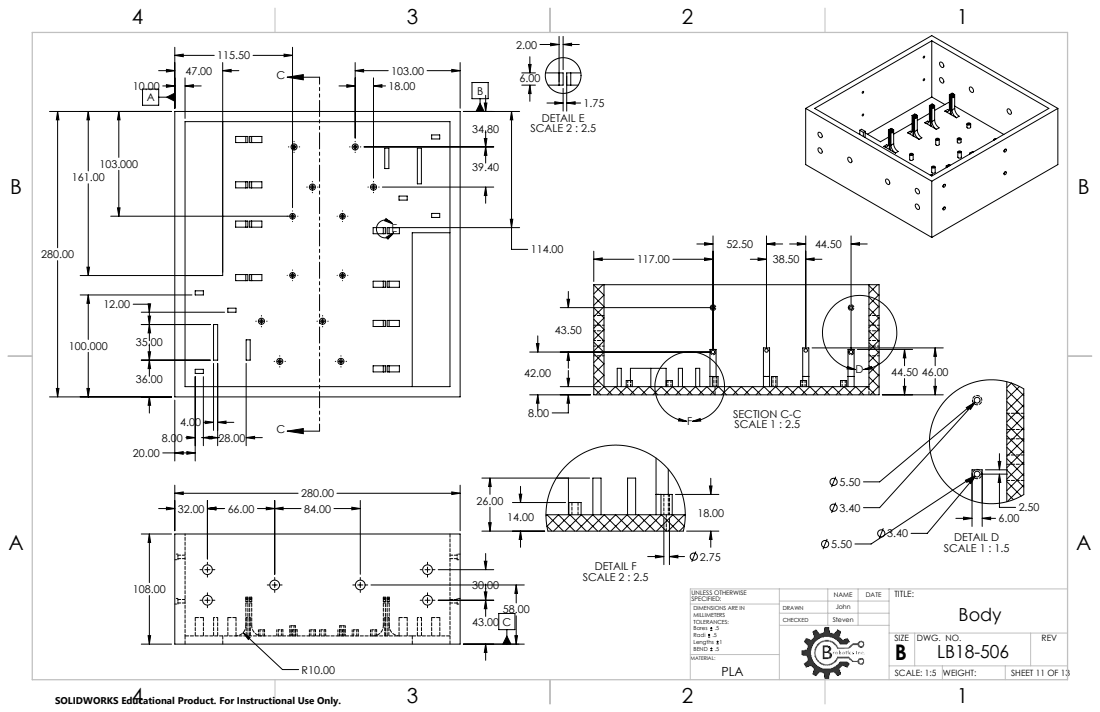
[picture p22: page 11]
SECTION C-C; SCALE 1 : 2.5; DETAIL D SCALE 1 : 1.5; DETAIL E SCALE 2 : 2.5; DETAIL F SCALE 2 : 2.5; DIMENSIONS ARE IN; Bores .5 Radi .5 Lengths 1 BEND .5

UNLESS OTHERWISE SPECIFIED: | | NAME | DATE | TITLE: Body

DRAWN | Steven John

SIZE B | DWG. NO. LB18-506 | REV

SCALE: 1:5 | WEIGHT:

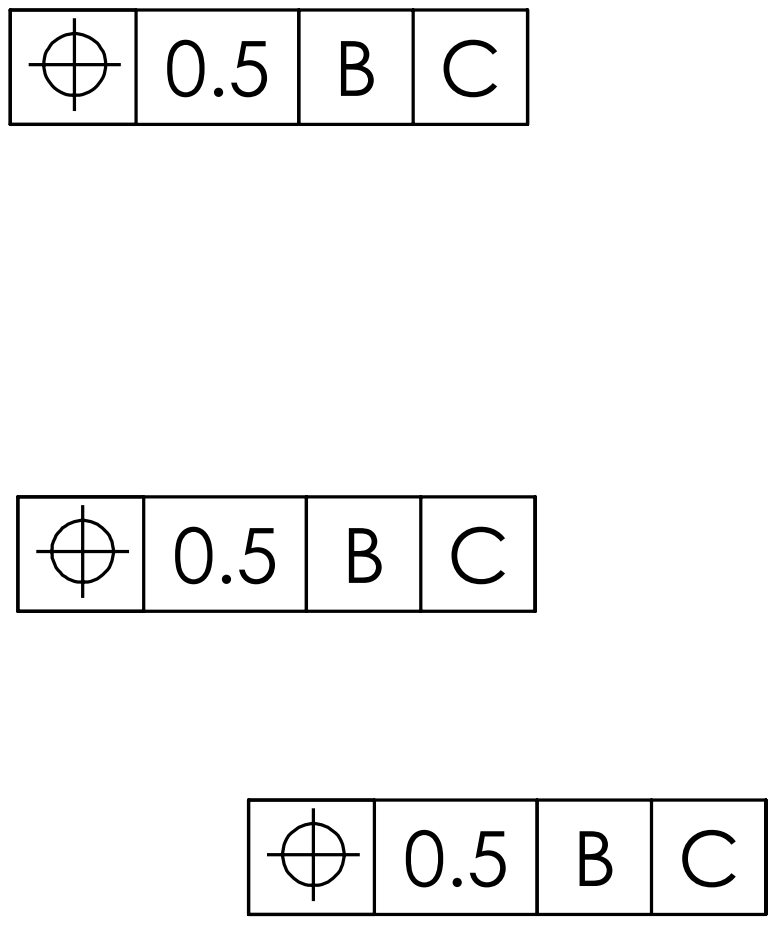
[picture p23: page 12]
DIMENSIONS ARE IN; Bores .5 Radi .5 Lengths 1 BEND .5

SPECIFIED: | | NAME UNLESS OTHERWISE | DATE | TITLE: COVER, MOTOR

DRAWN | Steven John
CHECKED

SIZE B | DWG. NO. LB18-508 | REV

SCALE: 2:3 | WEIGHT:

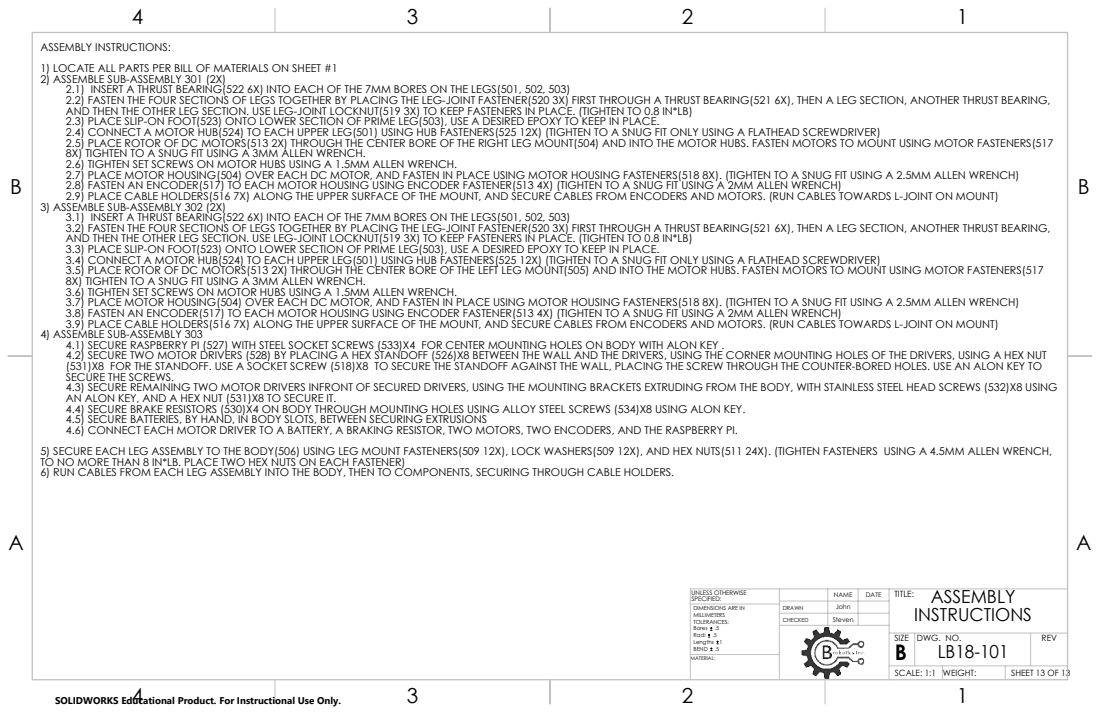
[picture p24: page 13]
DIMENSIONS ARE IN; Bores .5 Radi .5 Lengths 1 BEND .5

ASSEMBLY INSTRUCTIONS:
1) LOCATE ALL PARTS PER BILL OF MATERIALS ON SHEET #1
2) ASSEMBLE SUB-ASSEMBLY 301 (2X)
2.1) INSERT A THRUST BEARING(522 6X) INTO EACH OF THE 7MM BORES ON THE LEGS(501, 502, 503)
2.2) FASTEN THE FOUR SECTIONS OF LEGS TOGETHER BY PLACING THE LEG-JOINT FASTENER(520 3X) FIRST THROUGH A THRUST BEARING(521 6X), THEN A LEG SECTION, ANOTHER THRUST BEARING,
AND THEN THE OTHER LEG SECTION. USE LEG-JOINT LOCKNUT(519 3X) TO KEEP FASTENERS IN PLACE. (TIGHTEN TO 0.8 IN*LB)
2.3) PLACE SLIP-ON FOOT(523) ONTO LOWER SECTION OF PRIME LEG(503), USE A DESIRED EPOXY TO KEEP IN PLACE.
2.4) CONNECT A MOTOR HUB(524) TO EACH UPPER LEG(501) USING HUB FASTENERS(525 12X) (TIGHTEN TO A SNUG FIT ONLY USING A FLATHEAD SCREWDRIVER)
2.5) PLACE ROTOR OF DC MOTORS(513 2X) THROUGH THE CENTER BORE OF THE RIGHT LEG MOUNT(504) AND INTO THE MOTOR HUBS. FASTEN MOTORS TO MOUNT USING MOTOR FASTENERS(517
8X) TIGHTEN TO A SNUG FIT USING A 3MM ALLEN WRENCH.
2.6) TIGHTEN SET SCREWS ON MOTOR HUBS USING A 1.5MM ALLEN WRENCH.
2.7) PLACE MOTOR HOUSING(504) OVER EACH DC MOTOR, AND FASTEN IN PLACE USING MOTOR HOUSING FASTENERS(518 8X). (TIGHTEN TO A SNUG FIT USING A 2.5MM ALLEN WRENCH)
3) ASSEMBLE SUB-ASSEMBLY 302 (2X)
3.1) INSERT A THRUST BEARING(522 6X) INTO EACH OF THE 7MM BORES ON THE LEGS(501, 502, 503)
3.2) FASTEN THE FOUR SECTIONS OF LEGS TOGETHER BY PLACING THE LEG-JOINT FASTENER(520 3X) FIRST THROUGH A THRUST BEARING(521 6X), THEN A LEG SECTION, ANOTHER THRUST BEARING,
3.3) PLACE SLIP-ON FOOT(523) ONTO LOWER SECTION OF PRIME LEG(503), USE A DESIRED EPOXY TO KEEP IN PLACE.
3.4) CONNECT A MOTOR HUB(524) TO EACH UPPER LEG(501) USING HUB FASTENERS(525 12X) (TIGHTEN TO A SNUG FIT ONLY USING A FLATHEAD SCREWDRIVER)
3.5) PLACE ROTOR OF DC MOTORS(513 2X) THROUGH THE CENTER BORE OF THE LEFT LEG MOUNT(505) AND INTO THE MOTOR HUBS. FASTEN MOTORS TO MOUNT USING MOTOR FASTENERS(517
3.6) TIGHTEN SET SCREWS ON MOTOR HUBS USING A 1.5MM ALLEN WRENCH.
3.7) PLACE MOTOR HOUSING(504) OVER EACH DC MOTOR, AND FASTEN IN PLACE USING MOTOR HOUSING FASTENERS(518 8X). (TIGHTEN TO A SNUG FIT USING A 2.5MM ALLEN WRENCH)
3.8) FASTEN AN ENCODER(517) TO EACH MOTOR HOUSING USING ENCODER FASTENER(513 4X) (TIGHTEN TO A SNUG FIT USING A 2MM ALLEN WRENCH)
3.9) PLACE CABLE HOLDERS(516 7X) ALONG THE UPPER SURFACE OF THE MOUNT, AND SECURE CABLES FROM ENCODERS AND MOTORS. (RUN CABLES TOWARDS L-JOINT ON MOUNT)
4) ASSEMBLE SUB-ASSEMBLY 303
4.1) SECURE RASPBERRY PI (527) WITH STEEL SOCKET SCREWS (533)X4 FOR CENTER MOUNTING HOLES ON BODY WITH ALON KEY .
4.2) SECURE TWO MOTOR DRIVERS (528) BY PLACING A HEX STANDOFF (526)X8 BETWEEN THE WALL AND THE DRIVERS, USING THE CORNER MOUNTING HOLES OF THE DRIVERS, USING A HEX NUT
(531)X8 FOR THE STANDOFF. USE A SOCKET SCREW (518)X8 TO SECURE THE STANDOFF AGAINST THE WALL, PLACING THE SCREW THROUGH THE COUNTER-BORED HOLES. USE AN ALON KEY TO
SECURE THE SCREWS.
4.3) SECURE REMAINING TWO MOTOR DRIVERS INFRONT OF SECURED DRIVERS, USING THE MOUNTING BRACKETS EXTRUDING FROM THE BODY, WITH STAINLESS STEEL HEAD SCREWS (532)X8 USING
AN ALON KEY, AND A HEX NUT (531)X8 TO SECURE IT.
4.4) SECURE BRAKE RESISTORS (530)X4 ON BODY THROUGH MOUNTING HOLES USING ALLOY STEEL SCREWS (534)X8 USING ALON KEY.
4.5) SECURE BATTERIES, BY HAND, IN BODY SLOTS, BETWEEN SECURING EXTRUSIONS
4.6) CONNECT EACH MOTOR DRIVER TO A BATTERY, A BRAKING RESISTOR, TWO MOTORS, TWO ENCODERS, AND THE RASPBERRY PI.
5) SECURE EACH LEG ASSEMBLY TO THE BODY(506) USING LEG MOUNT FASTENERS(509 12X), LOCK WASHERS(509 12X), AND HEX NUTS(511 24X). (TIGHTEN FASTENERS USING A 4.5MM ALLEN WRENCH,
TO NO MORE THAN 8 IN*LB. PLACE TWO HEX NUTS ON EACH FASTENER)
6) RUN CABLES FROM EACH LEG ASSEMBLY INTO THE BODY, THEN TO COMPONENTS, SECURING THROUGH CABLE HOLDERS.

2.8) FASTEN AN ENCODER(517) TO EACH MOTOR HOUSING USING ENCODER FASTENER(513 4X) (TIGHTEN TO A SNUG FIT USING A 2MM ALLEN WRENCH)
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

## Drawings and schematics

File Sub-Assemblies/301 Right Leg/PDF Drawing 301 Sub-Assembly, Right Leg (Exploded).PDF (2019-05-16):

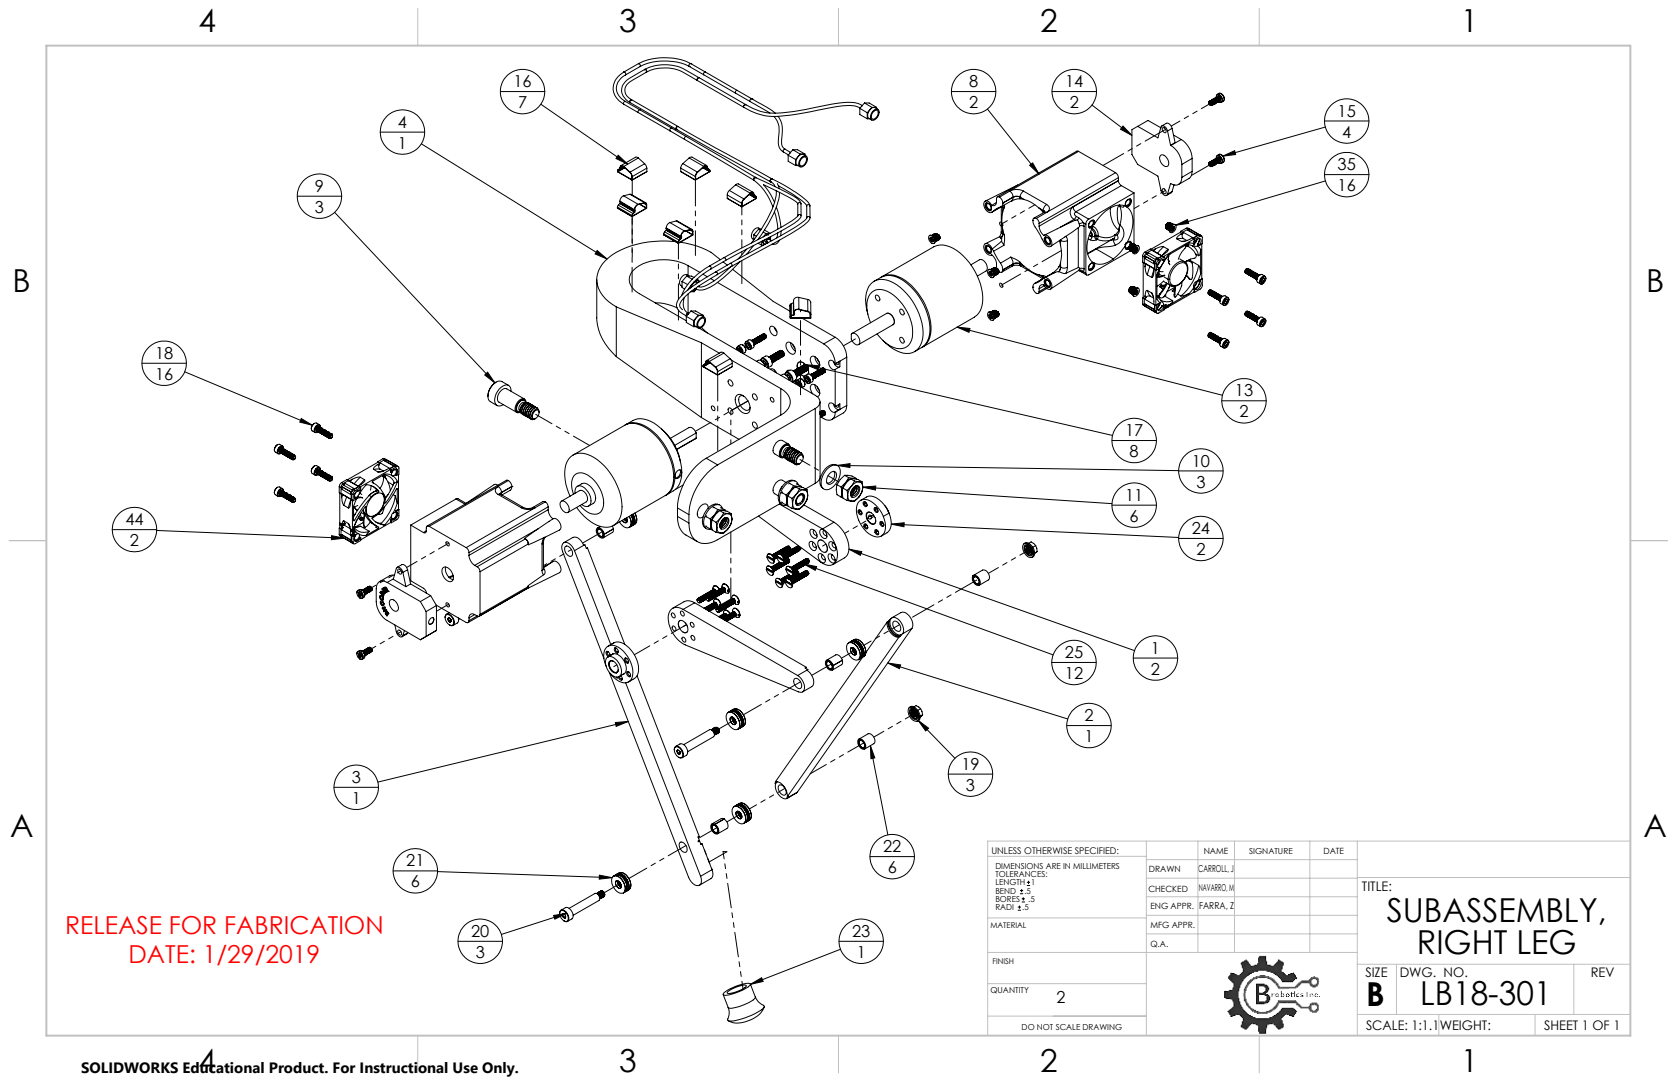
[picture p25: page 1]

UNLESS OTHERWISE SPECIFIED: | | NAME | SIGNATURE | DATE
DIMENSIONS ARE IN MILLIMETERS TOLERANCES: LENGTH 1 BEND .5 BORES .5 RADI .5 | DRAWN | CARROLL, J

CHECKED | NAVARRO, M | | | TITLE: SUBASSEMBLY, RIGHT LEG
ENG APPR. | FARRA, Z

RELEASE FOR FABRICATION
DATE: 1/29/2019

MATERIAL | MFG APPR.

FINISH

SIZE B | DWG. NO. LB18-301 | REV

DO NOT SCALE DRAWING | | SCALE: 1:1.1WEIGHT: | SHEET 1 OF 1

SOLIDWORKS Educational Product. For Instructional Use Only.

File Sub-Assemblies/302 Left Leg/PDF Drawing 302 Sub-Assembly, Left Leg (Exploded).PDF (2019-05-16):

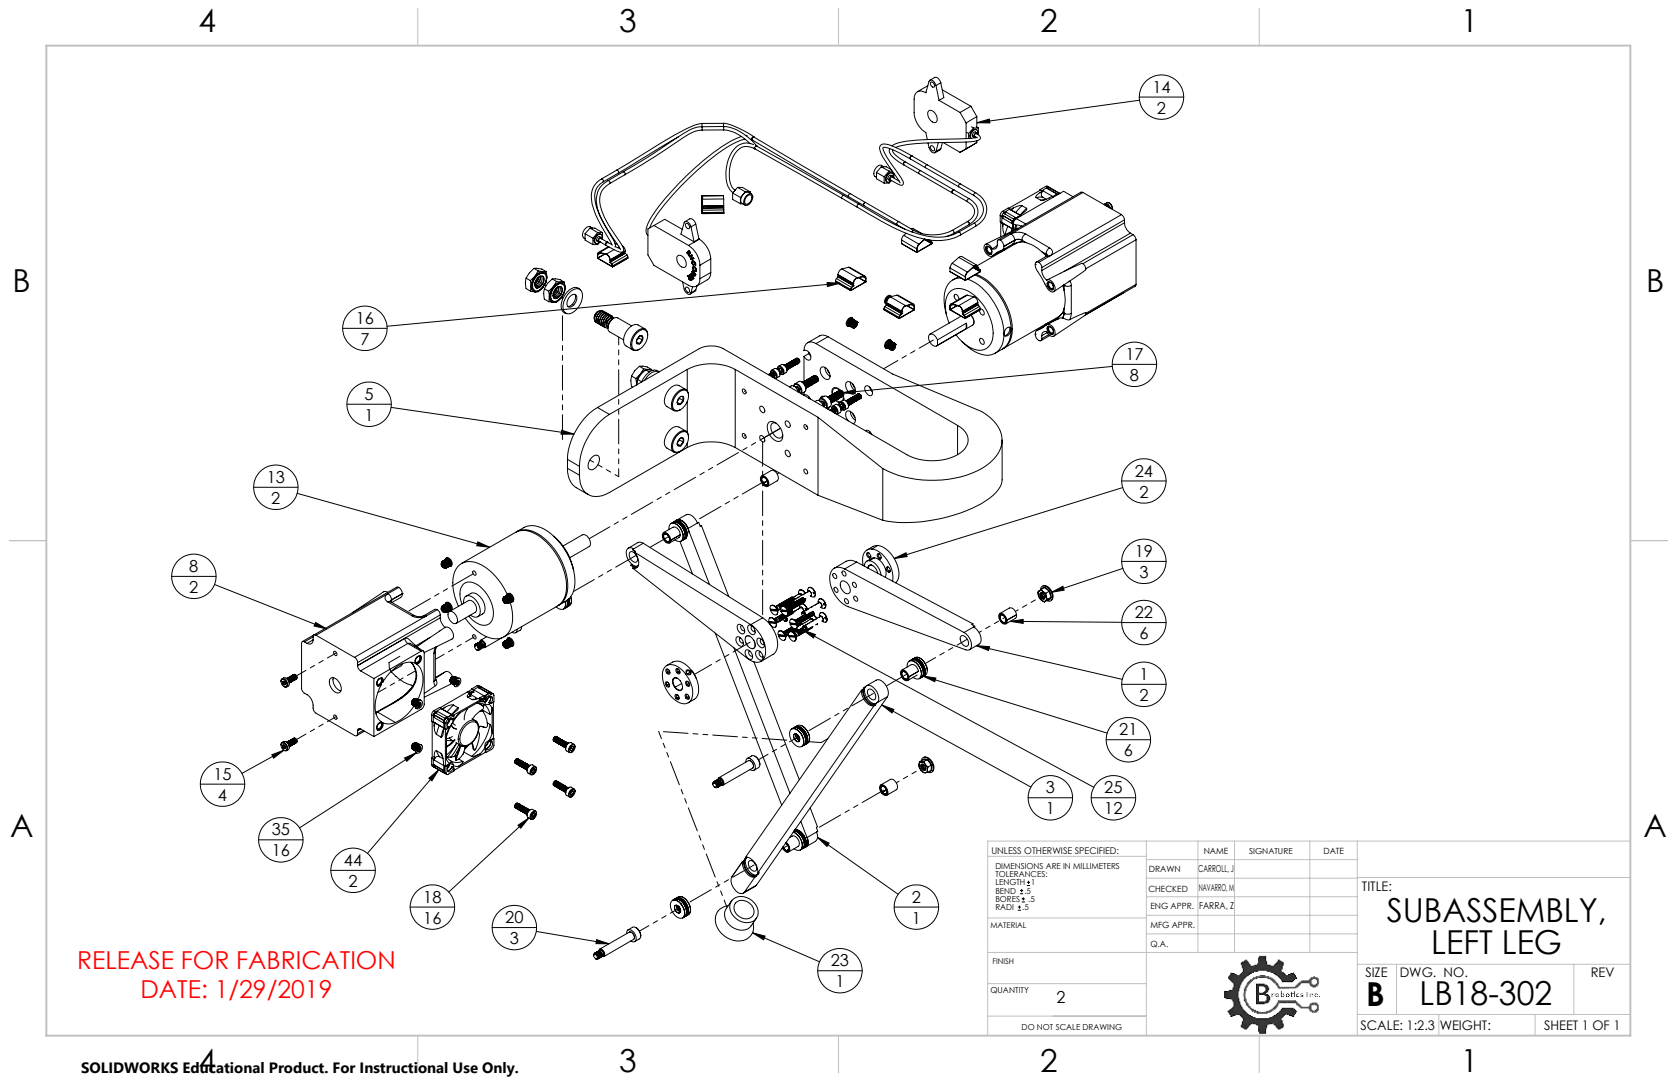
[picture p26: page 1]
RELEASE FOR FABRICATION DATE: 1/29/2019

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

CHECKED | NAVARRO, M | | | TITLE: SUBASSEMBLY, LEFT LEG
ENG APPR. | FARRA, Z

MATERIAL | MFG APPR.

FINISH

SIZE B | DWG. NO. LB18-302 | REV

DO NOT SCALE DRAWING | | SCALE: 1:2.3 WEIGHT: | SHEET 1 OF 1

SOLIDWORKS Educational Product. For Instructional Use Only.

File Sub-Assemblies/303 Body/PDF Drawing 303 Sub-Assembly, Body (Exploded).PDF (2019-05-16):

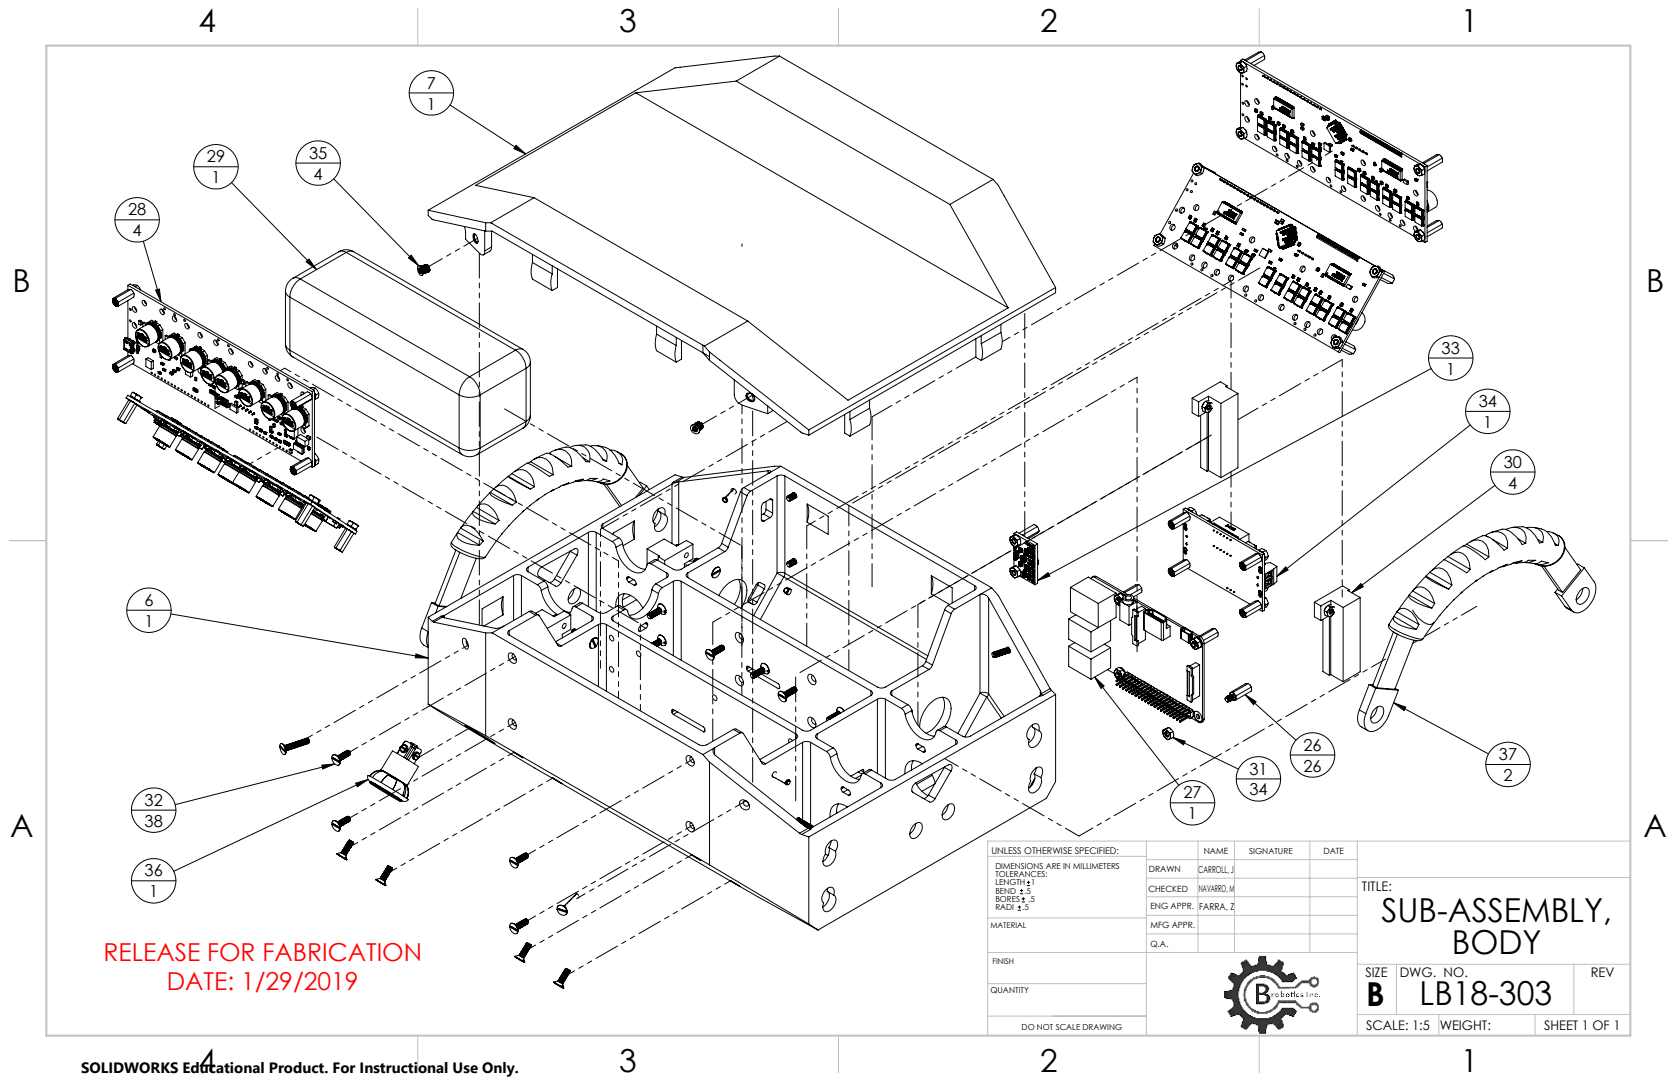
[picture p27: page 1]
RELEASE FOR FABRICATION DATE: 1/29/2019

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

CHECKED | NAVARRO, M | | | TITLE: SUB-ASSEMBLY, BODY

ENG APPR. | FARRA, Z

MATERIAL | MFG APPR.

FINISH

SIZE B | DWG. NO. LB18-303 | REV

DO NOT SCALE DRAWING | | SCALE: 1:5 | WEIGHT: | SHEET 1 OF 1

SOLIDWORKS Educational Product. For Instructional Use Only.

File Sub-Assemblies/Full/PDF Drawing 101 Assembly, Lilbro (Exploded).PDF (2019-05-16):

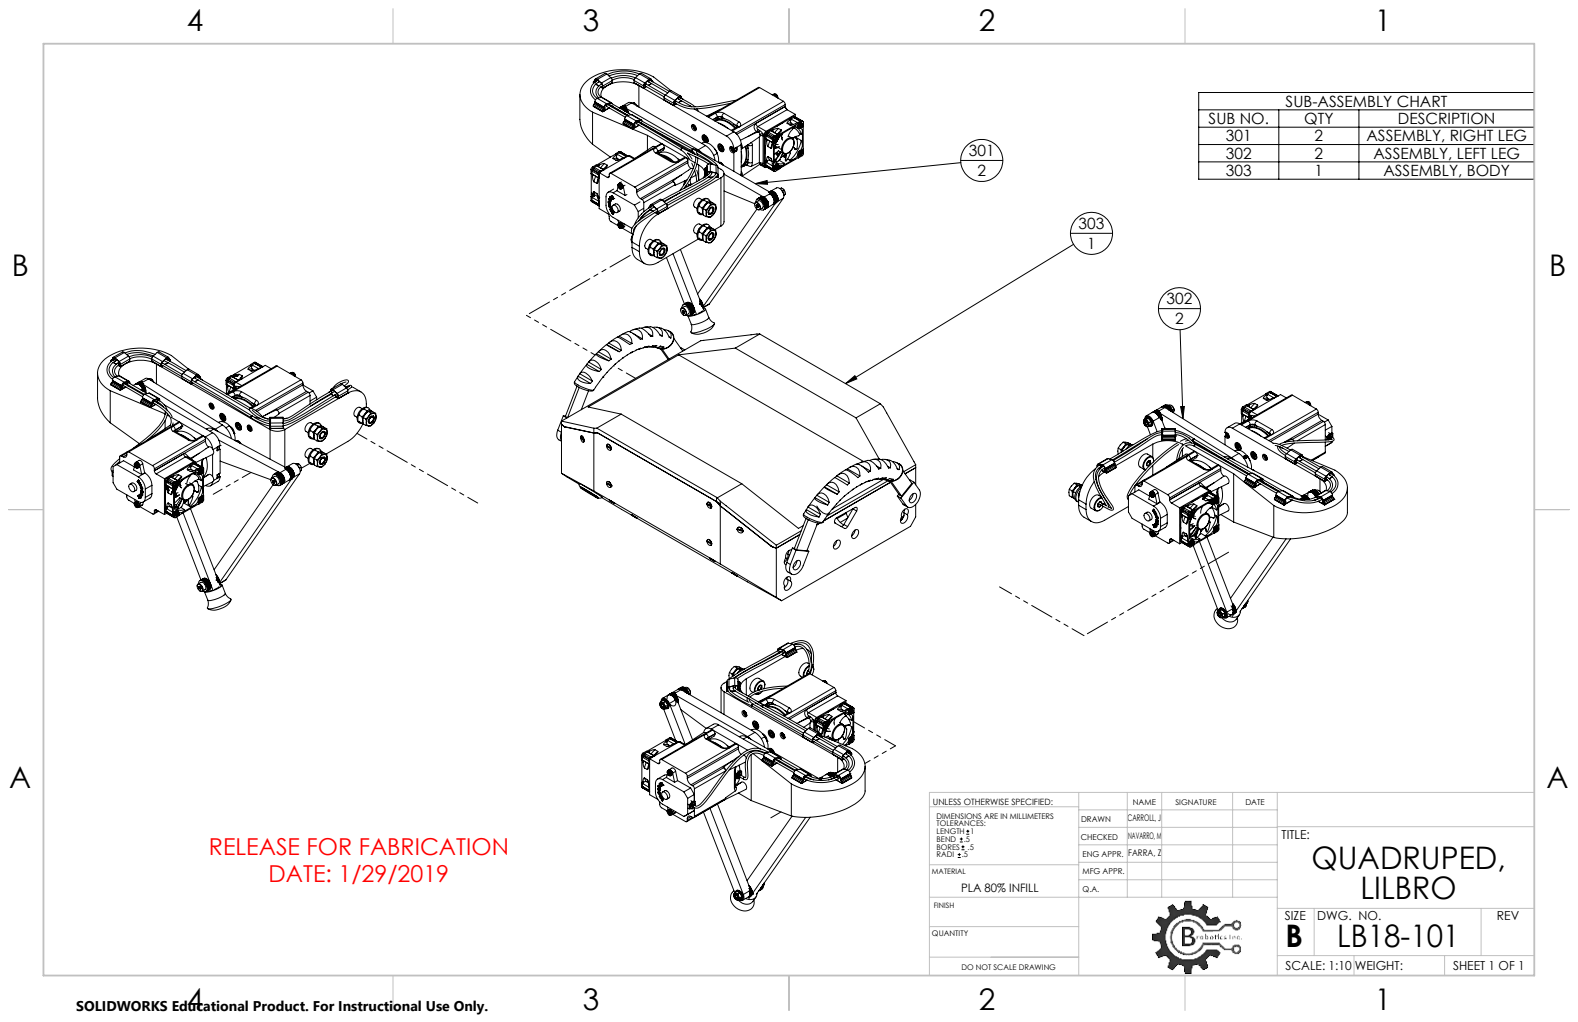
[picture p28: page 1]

SUB-ASSEMBLY CHART

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

CHECKED | NAVARRO, M | | | TITLE: QUADRUPED, LILBRO
ENG APPR. | FARRA, Z

RELEASE FOR FABRICATION
DATE: 1/29/2019

MATERIAL PLA 80% INFILL | MFG APPR.

FINISH

SIZE B | DWG. NO. LB18-101 | REV

DO NOT SCALE DRAWING | | SCALE: 1:10 WEIGHT: | SHEET 1 OF 1

SOLIDWORKS Educational Product. For Instructional Use Only.

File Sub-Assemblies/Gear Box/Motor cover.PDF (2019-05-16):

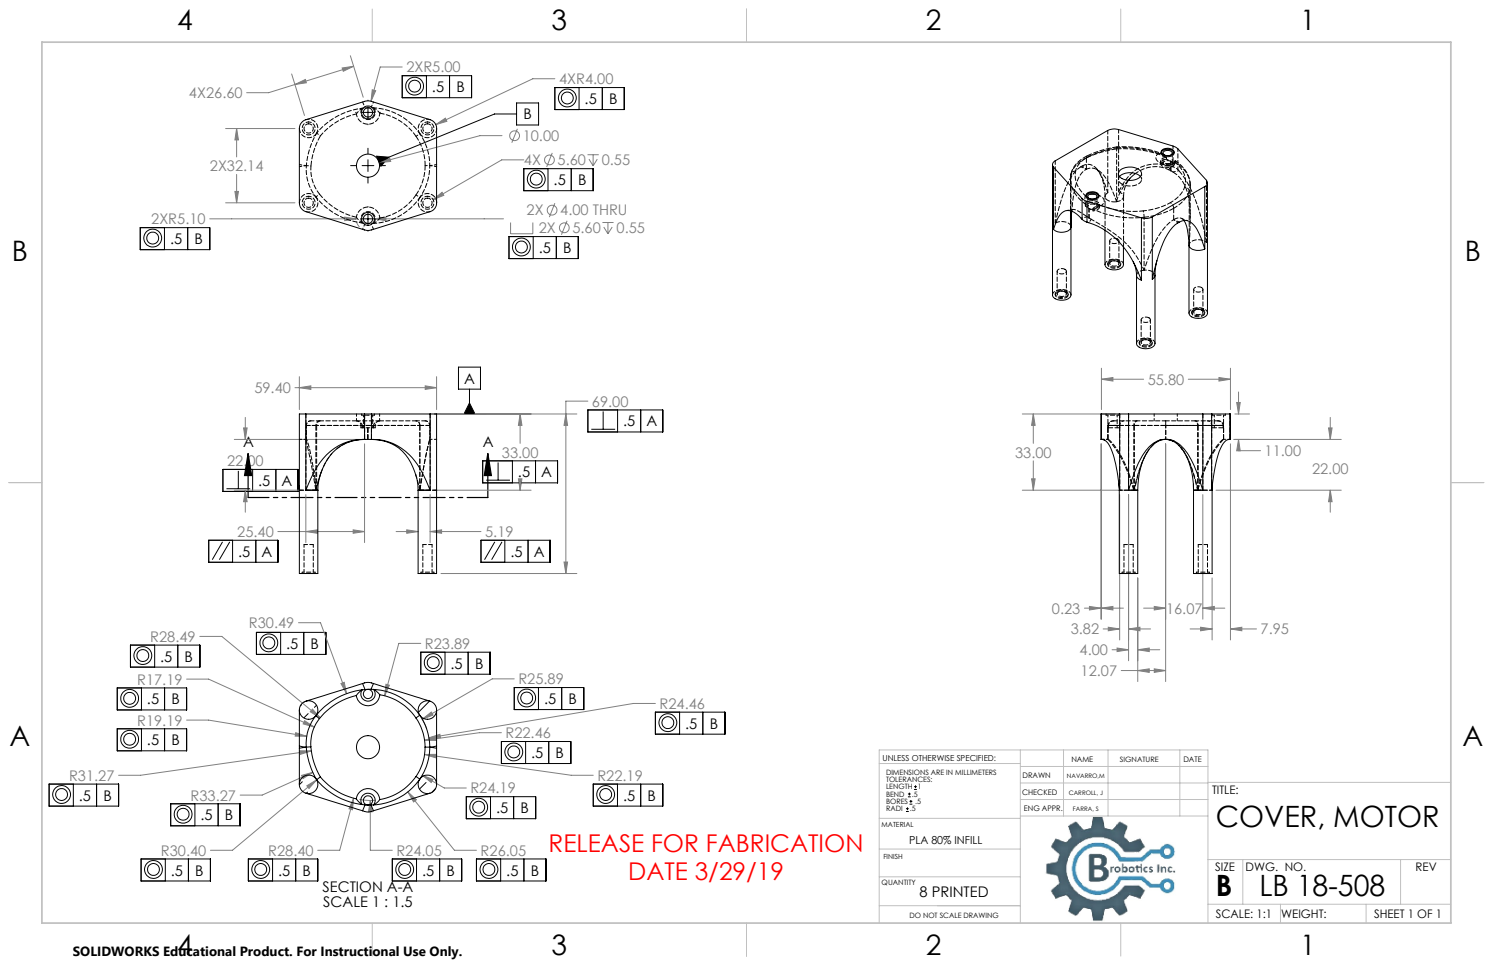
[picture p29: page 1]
2X 4.00 THRU 2X 5.60 0.55; SECTION A-A SCALE 1 : 1.5; RELEASE FOR FABRICATION DATE 3/29/19; PLA 80% INFILL; 8 PRINTED

UNLESS OTHERWISE SPECIFIED: | | NAME | SIGNATURE | DATE
DIMENSIONS ARE IN MILLIMETERS TOLERANCES: LENGTH 1 BEND .5 BORES .5 RADI .5 | DRAWN | NAVARRO,M

CHECKED | CARROLL, J | | | TITLE: COVER, MOTOR

ENG APPR. | FARRA, S

SIZE B | DWG. NO. LB 18-508 | REV

DO NOT SCALE DRAWING | | SCALE: 1:1 | WEIGHT: | SHEET 1 OF 1

SOLIDWORKS Educational Product. For Instructional Use Only.

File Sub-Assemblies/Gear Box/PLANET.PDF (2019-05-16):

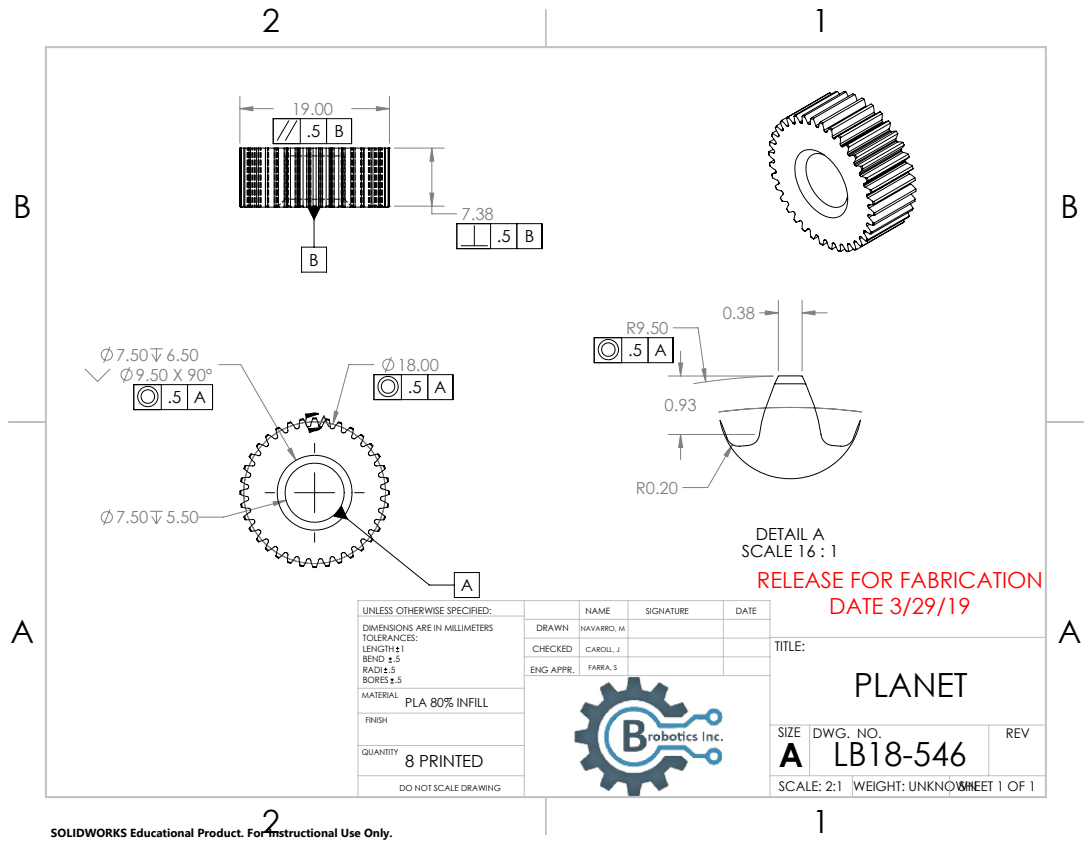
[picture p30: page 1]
PLA 80% INFILL; 8 PRINTED

DETAIL A
SCALE 16 : 1
RELEASE FOR FABRICATION
DATE 3/29/19

UNLESS OTHERWISE SPECIFIED: | | NAME | SIGNATURE | DATE
DIMENSIONS ARE IN MILLIMETERS TOLERANCES: LENGTH 1 BEND .5 RADI .5 BORES .5 | DRAWN | NAVARRO, M

CHECKED | CAROLL, J | | | TITLE: PLANET

ENG APPR. | FARRA, S

SIZE A | DWG. NO. LB18-546 | REV

DO NOT SCALE DRAWING | | SCALE: 2:1 | WEIGHT: UNKNOWN | SHEET 1 OF 1

SOLIDWORKS Educational Product. For Instructional Use Only.

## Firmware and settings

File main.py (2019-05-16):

import time as time_
import os, struct, array
from fcntl import ioctl
import robot
import math
import numpy as np
import odrive
import globals
import sys
import threading
import leds

print('Finding drivers...')

globals.initialize()
lilbro = robot.robot()
led = leds.leds()

LedThrd = threading.Thread(target = led.main)
LedThrd.daemon = True
LedThrd.start()

lilbro.findDrivers('388937803437','2061376D3548','206A3379304B','385337753437')

print('Drivers found',lilbro.getDriver1(),' ',lilbro.getDriver2(),' ',lilbro.getDriver3(),' ',lilbro.getDriver4())

lilbro.setFootTrajectory(0.165,0.135/0.165,15,0.4,1)
lilbro.setFootTrajectory(0.165,0.135/0.165,15,0.4,2)

alpha2 = []
legParms = []
alpha2m = []
alpha2_s = []
legParmsm = []
legParms_s = []
l_m = np.linspace(0.17,0.14,6)
l = np.linspace(0.135,0.275,50)
l_squat = np.linspace(0.14,0.17,20)

alpha = 0
l1 = 0.1
l2 = 0.22
theta1 = []
theta2 = []
theta1m = []
theta2m = []
theta1_s = []
theta2_s = []
n = 12
nh = 7

posGain = 85
velGain = 0.00055
velIntGain = 0.5*100*velGain

lilbro.setStates(1)
lilbro.setPGains(posGain)
lilbro.setVelGains(velGain)
lilbro.setVelIntGains(velIntGain)
lilbro.setTrajAll(150000,105000,105000,0)
lilbro.setVelLims(200000)

# Joystick Code --------------------------------------

# JS state storage
axis_states = {}
button_states = {}

# These constants were borrowed from linux/input.h
axis_names = {
    0x00 : 'x',
    0x01 : 'y',
    0x02 : 'z',
    0x03 : 'rx',
    0x04 : 'ry',
    0x05 : 'rz',
    0x06 : 'trottle',
    0x07 : 'rudder',
    0x08 : 'wheel',
    0x09 : 'gas',
    0x0a : 'brake',
    0x10 : 'hat0x',
    0x11 : 'hat0y',
    0x12 : 'hat1x',
    0x13 : 'hat1y',
    0x14 : 'hat2x',
    0x15 : 'hat2y',
    0x16 : 'hat3x',
    0x17 : 'hat3y',
    0x18 : 'pressure',
    0x19 : 'distance',
    0x1a : 'tilt_x',
    0x1b : 'tilt_y',
    0x1c : 'tool_width',
    0x20 : 'volume',
    0x28 : 'misc',
}

button_names = {
    0x120 : 'trigger',
    0x121 : 'thumb',
    0x122 : 'thumb2',
    0x123 : 'top',
    0x124 : 'top2',
    0x125 : 'pinkie',
    0x126 : 'base',
    0x127 : 'base2',
    0x128 : 'base3',
    0x129 : 'base4',
    0x12a : 'base5',
    0x12b : 'base6',
    0x12f : 'dead',
    0x130 : 'a',
    0x131 : 'b',
    0x132 : 'c',
    0x133 : 'x',
    0x134 : 'y',
    0x135 : 'z',
    0x136 : 'tl',
    0x137 : 'tr',
    0x138 : 'tl2',
    0x139 : 'tr2',
    0x13a : 'select',
    0x13b : 'start',
    0x13c : 'mode',
    0x13d : 'thumbl',
    0x13e : 'thumbr',

    0x220 : 'dpad_up',
    0x221 : 'dpad_down',
    0x222 : 'dpad_left',
    0x223 : 'dpad_right',

    # XBox 360 controller uses these codes.
    0x2c0 : 'dpad_left',
    0x2c1 : 'dpad_right',
    0x2c2 : 'dpad_up',
    0x2c3 : 'dpad_down',
}

axis_map = []
button_map = []

def ctrl_map(x,in_min,in_max,out_min,out_max):
    return (x-in_min)*(out_max-out_min)/(in_max-in_min)+out_min

# Open the joystick device.
fn = '/dev/input/js0'
print('Opening %s...' % fn)

try:
    jsdev = open(fn, 'rb')

except IOError:
    print('No PS3 Controller connected')
    print('Please press the PS button to connect...')

    while True:
        if os.path.exists('/dev/input/js0'):
            print('Controller connected')

            jsdev = open(fn, 'rb')
            break

# Get the device name.

buf = bytearray(63)
# buf = array.array('u', ['\0'] * 64)
ioctl(jsdev, 0x80006a13 + (0x10000 * len(buf)), buf) # JSIOCGNAME(len)
# Get rid of random padding
buf = buf.rstrip(b'\0')
js_name = str(buf, encoding='utf-8')
print('Device name: %s' % js_name)

# Get number of axes and buttons.
buf = array.array('B', [0])
ioctl(jsdev, 0x80016a11, buf) # JSIOCGAXES
num_axes = buf[0]

buf = array.array('B', [0])
ioctl(jsdev, 0x80016a12, buf) # JSIOCGBUTTONS
num_buttons = buf[0]

# Get the axis map.
buf = array.array('B', [0] * 0x40)
ioctl(jsdev, 0x80406a32, buf) # JSIOCGAXMAP

for axis in buf[:num_axes]:
    axis_name = axis_names.get(axis, 'unknown(0x%02x)' % axis)
    axis_map.append(axis_name)
    axis_states[axis_name] = 0.0

# Get the button map.
buf = array.array('H', [0] * 200)
ioctl(jsdev, 0x80406a34, buf) # JSIOCGBTNMAP

for btn in buf[:num_buttons]:
    btn_name = button_names.get(btn, 'unknown(0x%03x)' % btn)
    button_map.append(btn_name)
    button_states[btn_name] = 0
    
def readJS():
    global armed
    global setpt_on
    global angle_cnt
    global jsdev
    global inTime
    global varTime
    global trigValue, map1, map2
    global gain
    global pos_0
    global pos_1
    global sweepOn
    global encFlag, dataFlag, dataSaved, R1Flag, lock 
    global offset, walkDir
    global paths, trotPath, thPath, squatOn
    global pathOn, manSquat, pathCalc, trotCalc, trotOn, thOn, thCalc, marchOn
    global off1, off2, off3, off4
    global standby
    global walking
    walking = 0
    standby = 1
    walkDir = 1
    pathOn = 0
    trotOn = 0
    thOn = 0
    squatOn = 0
    pathCalc = 0
    trotCalc = 0
    thCalc = 0
    map1 = len(l_m)/2
    map2 = len(l_m)/2
    marchOn = 0
    paths = []
    trotPath = []
    thPath = []
    offset = []
    encFlag = 1
    dataFlag = 1
    R1Flag = 0
    lock = 1
    dataSaved = 0
    sweepOn = 0
    gain = 20
    walkPath = 0
    pos_0 = -1000
    pos_1 = -1000
    trigValue = 0
    off1 = []
    off2 = []
    off3 = []
    off4 = []
    armed = False
    while True:

        # Read the joystick
        try:
            evbuf = jsdev.read(8)

        # If the controller disconnects during operation, turn off motors and wait for reconnect
        except IOError:
            lilbro.setState(lilbro.driver1,1)
            lilbro.setState(lilbro.driver2,1)
            lilbro.setState(lilbro.driver3,1)
            lilbro.setState(lilbro.driver4,1)

            print('No PS3 Controller connected')
            print('Please press the PS button to connect...')

            while True:
                if os.path.exists('/dev/input/js0'):
                    print('Controller connected')

                    evbuf = jsdev.read(8)
                    break

        if evbuf:
            time, value, type, number = struct.unpack('IhBB', evbuf)

            # Determine if evbuf is the initial value
            if type & 0x80:
                # print((initial)),
                continue

            # Determine if evbuf is a button
            if type & 0x01:
                button = button_map[number]
                if button:
                   button_states[button] = value
#                    # Print states (debug only)
#                    print(value)
#                   if value:
#                        print("%s pressed" % (button))
#                    else:
#                        print("%s released" % (button))

            if button_states['start'] and (armed == False):
                lilbro.setState(lilbro.driver1,8)
                lilbro.setState(lilbro.driver2,8)
                lilbro.setState(lilbro.driver3,8)
                lilbro.setState(lilbro.driver4,8)
                armed = True
                print('Motors Armed!')

            if button_states['select'] and (armed == True):
                lilbro.setState(lilbro.driver1,1)
                lilbro.setState(lilbro.driver2,1)
                lilbro.setState(lilbro.driver3,1)
                lilbro.setState(lilbro.driver4,1)
                armed = False
                sweepOn = 0
                print("Motors Unarmed!")
                
            if button_states['dpad_up'] and lock == 0:   
                lilbro.addPGain(lilbro.driver1,10)
                lilbro.addPGain(lilbro.driver4,10)
                print('Front P Gain is ',lilbro.getPGain(lilbro.driver1.axis0))

            if button_states['dpad_down'] and lock == 0:
                lilbro.addPGain(lilbro.driver1,-10)
                lilbro.addPGain(lilbro.driver4,-10)
                print('Front P Gain is ',lilbro.getPGain(lilbro.driver1.axis0))

            if button_states['dpad_right'] and lock == 0:   
                lilbro.addPGain(lilbro.driver2,10)
                lilbro.addPGain(lilbro.driver3,10)
                print('Back P Gain is ',lilbro.getPGain(lilbro.driver2.axis0))

            if button_states['dpad_left'] and lock == 0:
                lilbro.addPGain(lilbro.driver2,-10)
                lilbro.addPGain(lilbro.driver3,-10)
                print('Back P Gain is ',lilbro.getPGain(lilbro.driver2.axis0))

            if button_states['thumbr']:
                lock = 0
                print("lock OFF")

            if button_states['thumbl']:
                lock = 1
                print("lock ON")
                print("Bus voltage is ",lilbro.getBusVoltage())

            if button_states['tr']:
                if value:
                    globals.modeStat = 1
                    if button_states['dpad_up']:
                        if(globals.modeNum == 7):
                            globals.modeNum = 7
                        else:
                            globals.modeNum = globals.modeNum + 1
                            globals.decMode = globals.modeNum + 1
                    elif button_states['dpad_down']:
                        if(globals.modeNum == 3):
                            globals.modeNum = 3
                        else:
                            globals.modeNum = globals.modeNum - 1
                            globals.decMode = globals.modeNum + 1
                    
                    if button_states['a']:
                        standby = 0
                        globals.modeStat = 0


            if button_states['tl']:
                if button_states['b']:
                    if(encFlag == 1):
                        print("Encoder angle offsets measurement ready!");
                        lilbro.setStates(1) 
                        armed = 0
                                
                    elif(encFlag == -1):
                        print("Encoder angle offsets measured!")
                        offset = lilbro.getEncOffsets()
                        print("Encoder offsets are ",offset)
                                
                    encFlag = encFlag*-1

                if button_states['dpad_left']:
                    lilbro.addAccelLims(-5000)
                    print('Accel lims are ',lilbro.driver1.axis0.trap_traj.config.accel_limit)

                if button_states['dpad_right']:
                    lilbro.addAccelLims(5000)
                    print('Accel lims are ',lilbro.driver1.axis0.trap_traj.config.accel_limit)

            if button_states['b']:
                if value:
                    standby = 1
                    print('Standby On')

            if button_states['y'] and globals.modeNum == 7:
                if(walkDir == 1):
                    print("Walk Backwards!");
                elif(walkDir == -1):
                    print("Walk Forward!")
                walkDir = walkDir*-1

            if button_states['x'] and armed == 1 and standby == 1:
                if value:
                    print("Home postion")
                    lilbro.driver1.axis0.controller.move_to_pos(lilbro.toMotor(lilbro.toCount(-50+offset[0])))
                    lilbro.driver1.axis1.controller.move_to_pos(lilbro.toMotor(lilbro.toCount(-50+offset[1])))
                    lilbro.driver2.axis0.controller.move_to_pos(lilbro.toMotor(lilbro.toCount(-50+offset[2])))
                    lilbro.driver2.axis1.controller.move_to_pos(lilbro.toMotor(lilbro.toCount(-50+offset[3])))
                    lilbro.driver3.axis0.controller.move_to_pos(lilbro.toMotor(lilbro.toCount(50-1*offset[4])))
                    lilbro.driver3.axis1.controller.move_to_pos(lilbro.toMotor(lilbro.toCount(50-1*offset[5])))
                    lilbro.driver4.axis0.controller.move_to_pos(lilbro.toMotor(lilbro.toCount(50-1*offset[6])))
                    lilbro.driver4.axis1.controller.move_to_pos(lilbro.toMotor(lilbro.toCount(50-1*offset[7])))                    

            if type & 0x02:
                fvalue = value / 32767.0
                axis = axis_map[number]
                if(axis == 'y'):
                    fvalue = (value / 32767.0) * -1
                    trigValue = fvalue
                    walking = fvalue
                    axis_states[axis] = fvalue

# Start the readJS thread. Reads joystick in the "background"
readJSThrd = threading.Thread(target=readJS)
readJSThrd.daemon = True
readJSThrd.start()

for i in range(len(l)):
    alpha2.append(math.acos((((l1**2)+((l[i])**2)-(l2**2))/(2*l1*l[i]))))
    alpha1 = alpha - math.pi/2
    legParms.append(lilbro.symmetric(alpha1,alpha2[i],l1,l2))
    theta1.append(math.atan2(-legParms[i][1][0],legParms[i][1][1]))
    theta2.append(math.atan2(legParms[i][2][0],legParms[i][2][1]))

for i in range(len(l_m)):
    alpha2m.append(math.acos((((l1**2)+((l_m[i])**2)-(l2**2))/(2*l1*l_m[i]))))
    alpha1m = alpha - math.pi/2
    legParmsm.append(lilbro.symmetric(alpha1m,alpha2m[i],l1,l2))
    theta1m.append(math.atan2(-legParmsm[i][1][0],legParmsm[i][1][1]))
    theta2m.append(math.atan2(legParmsm[i][2][0],legParmsm[i][2][1]))

for k in range(len(l_squat)):
    alpha2_s.append(math.acos((((l1**2)+((l_squat[k])**2)-(l2**2))/(2*l1*l_squat[k]))))
    alpha1_s = alpha - math.pi/2
    legParms_s.append(lilbro.symmetric(alpha1_s,alpha2_s[k],l1,l2))
    theta1_s.append(math.atan2(-legParms_s[k][1][0],legParms_s[k][1][1]))
    theta2_s.append(math.atan2(legParms_s[k][2][0],legParms_s[k][2][1]))

offset = [31,18,64.5,40.5,61,14.5,80,56]

stalpha2 = math.acos((((l1**2)+((0.17**2)-(l2**2))/(2*l1*0.17))))
stlegParms = lilbro.symmetric(-math.pi/2,stalpha2,l1,l2)
sttheta1 = math.atan2(-stlegParms[1][0],stlegParms[1][1])
sttheta2 = math.atan2(stlegParms[2][0],stlegParms[2][1])

while True:
    try:

        if(standby == 1):
            globals.error = lilbro.isError()
            time_.sleep(0.0005)
        else:
            if(armed == 1 and globals.modeStat == 1):
                lilbro.driver1.axis0.controller.move_to_pos(lilbro.toMotor(lilbro.toCount(-50+offset[0])))
                lilbro.driver1.axis1.controller.move_to_pos(lilbro.toMotor(lilbro.toCount(-50+offset[1])))
                lilbro.driver2.axis0.controller.move_to_pos(lilbro.toMotor(lilbro.toCount(-50+offset[2])))
                lilbro.driver2.axis1.controller.move_to_pos(lilbro.toMotor(lilbro.toCount(-50+offset[3])))
                lilbro.driver3.axis0.controller.move_to_pos(lilbro.toMotor(lilbro.toCount(50-1*offset[4])))
                lilbro.driver3.axis1.controller.move_to_pos(lilbro.toMotor(lilbro.toCount(50-1*offset[5])))
                lilbro.driver4.axis0.controller.move_to_pos(lilbro.toMotor(lilbro.toCount(50-1*offset[6])))
                lilbro.driver4.axis1.controller.move_to_pos(lilbro.toMotor(lilbro.toCount(50-1*offset[7])))

            if((globals.modeNum == 3 and armed ==1) and globals.modeStat == 0):
                lilbro.driver1.axis0.controller.move_to_pos(lilbro.toMotor(lilbro.toCount(-50+offset[0])))
                lilbro.driver1.axis1.controller.move_to_pos(lilbro.toMotor(lilbro.toCount(-50+offset[1])))
                lilbro.driver2.axis0.controller.move_to_pos(lilbro.toMotor(lilbro.toCount(-50+offset[2])))
                lilbro.driver2.axis1.controller.move_to_pos(lilbro.toMotor(lilbro.toCount(-50+offset[3])))
                lilbro.driver3.axis0.controller.move_to_pos(lilbro.toMotor(lilbro.toCount(50-1*offset[4])))
                lilbro.driver3.axis1.controller.move_to_pos(lilbro.toMotor(lilbro.toCount(50-1*offset[5])))
                lilbro.driver4.axis0.controller.move_to_pos(lilbro.toMotor(lilbro.toCount(50-1*offset[6])))
                lilbro.driver4.axis1.controller.move_to_pos(lilbro.toMotor(lilbro.toCount(50-1*offset[7])))


            if(globals.modeNum == 4 and armed == 1 and globals.modeStat == 0):
                
                for i in range(len(l_squat)):
                    if(globals.modeNum != 4 or armed == 0 or globals.modeStat == 1 or standby == 1):
                        break

                    posNow1 = lilbro.toMotor(lilbro.toCount(math.degrees(theta1_s[i])+offset[0]))
                    posNow2 = lilbro.toMotor(lilbro.toCount(math.degrees(theta2_s[i])+offset[1]))
                    posNow3 = lilbro.toMotor(lilbro.toCount(math.degrees(theta2_s[i])+offset[2]))
                    posNow4 = lilbro.toMotor(lilbro.toCount(math.degrees(theta1_s[i])+offset[3]))
                    posNow5 = lilbro.toMotor(lilbro.toCount(-math.degrees(theta2_s[i])-offset[4]))
                    posNow6 = lilbro.toMotor(lilbro.toCount(-math.degrees(theta1_s[i])-offset[5]))
                    posNow7 = lilbro.toMotor(lilbro.toCount(-math.degrees(theta1_s[i])-offset[6]))
                    posNow8 = lilbro.toMotor(lilbro.toCount(-math.degrees(theta2_s[i])-offset[7]))

                    lilbro.driver1.axis0.controller.move_to_pos(posNow1)
                    lilbro.driver1.axis1.controller.move_to_pos(posNow2)

                    lilbro.driver2.axis0.controller.move_to_pos(posNow3)
                    lilbro.driver2.axis1.controller.move_to_pos(posNow4)

                    lilbro.driver3.axis0.controller.move_to_pos(posNow5)
                    lilbro.driver3.axis1.controller.move_to_pos(posNow6)

                    lilbro.driver4.axis0.controller.move_to_pos(posNow7)
                    lilbro.driver4.axis1.controller.move_to_pos(posNow8)

                    print('Theta1,Theta2 =  ',lilbro.getAngle(lilbro.driver1))
            
                    time_.sleep(0.02)

                theta1f_s = np.flipud(theta1_s)
                theta2f_s = np.flipud(theta2_s)
                for j in range(len(l_squat)):
                    if(globals.modeNum != 4 or armed == 0 or globals.modeStat == 1 or standby == 1):
                        break
                            
                    posNow1 = lilbro.toMotor(lilbro.toCount(math.degrees(theta1f_s[j])+offset[0]))
                    posNow2 = lilbro.toMotor(lilbro.toCount(math.degrees(theta2f_s[j])+offset[1]))
                    posNow3 = lilbro.toMotor(lilbro.toCount(math.degrees(theta2f_s[j])+offset[2]))
                    posNow4 = lilbro.toMotor(lilbro.toCount(math.degrees(theta1f_s[j])+offset[3]))
                    posNow5 = lilbro.toMotor(lilbro.toCount(-math.degrees(theta2f_s[j])-offset[4]))
                    posNow6 = lilbro.toMotor(lilbro.toCount(-math.degrees(theta1f_s[j])-offset[5]))
                    posNow7 = lilbro.toMotor(lilbro.toCount(-math.degrees(theta1f_s[j])-offset[6]))
                    posNow8 = lilbro.toMotor(lilbro.toCount(-math.degrees(theta2f_s[j])-offset[7]))
                    lilbro.driver1.axis0.controller.move_to_pos(posNow1)
                    lilbro.driver1.axis1.controller.move_to_pos(posNow2)

                    lilbro.driver2.axis0.controller.move_to_pos(posNow3)
                    lilbro.driver2.axis1.controller.move_to_pos(posNow4)

                    lilbro.driver3.axis0.controller.move_to_pos(posNow5)
                    lilbro.driver3.axis1.controller.move_to_pos(posNow6)

                    lilbro.driver4.axis0.controller.move_to_pos(posNow7)
                    lilbro.driver4.axis1.controller.move_to_pos(posNow8)   

                    print('Theta1,Theta2 =  ',lilbro.getAngle(lilbro.driver1))
                    time_.sleep(0.02)

            if(globals.modeNum == 5 and armed == 1 and globals.modeStat == 0):
                
                for i in range(len(l)):
                    if(globals.modeNum != 5 or armed == 0 or globals.modeStat == 1 or standby == 1):
                        break

                    posNow1 = lilbro.toMotor(lilbro.toCount(math.degrees(theta1[i])+offset[0]))
                    posNow2 = lilbro.toMotor(lilbro.toCount(math.degrees(theta2[i])+offset[1]))
                    posNow3 = lilbro.toMotor(lilbro.toCount(math.degrees(theta2[i])+offset[2]))
                    posNow4 = lilbro.toMotor(lilbro.toCount(math.degrees(theta1[i])+offset[3]))
                    posNow5 = lilbro.toMotor(lilbro.toCount(-math.degrees(theta2[i])-offset[4]))
                    posNow6 = lilbro.toMotor(lilbro.toCount(-math.degrees(theta1[i])-offset[5]))
                    posNow7 = lilbro.toMotor(lilbro.toCount(-math.degrees(theta1[i])-offset[6]))
                    posNow8 = lilbro.toMotor(lilbro.toCount(-math.degrees(theta2[i])-offset[7]))

                    lilbro.driver1.axis0.controller.move_to_pos(posNow1)
                    lilbro.driver1.axis1.controller.move_to_pos(posNow2)

                    lilbro.driver2.axis0.controller.move_to_pos(posNow3)
                    lilbro.driver2.axis1.controller.move_to_pos(posNow4)

                    lilbro.driver3.axis0.controller.move_to_pos(posNow5)
                    lilbro.driver3.axis1.controller.move_to_pos(posNow6)

                    lilbro.driver4.axis0.controller.move_to_pos(posNow7)
                    lilbro.driver4.axis1.controller.move_to_pos(posNow8)

                    print('Theta1,Theta2 =  ',lilbro.getAngle(lilbro.driver1))
            
                    time_.sleep(0.015)

                standTime = time_.time()
                while(time_.time()-standTime <= 8):
                    if(globals.modeNum != 5 or armed == 0 or globals.modeStat == 1 or standby == 1):
                        break
                    time_.sleep(0.1)
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

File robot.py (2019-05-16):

#!usr/bin/python
# -----------------------------------
# An Odrive class used to control lil'Bro; an open source quadrupedal robot for UTSA's Robotics and Motion Laboratory
# 
#
# @authors Steven Farra, Emiliano Rodriguez 
# @version 1.0
# @since 2019-03-11
#
#
#
#
# @section license License
#
# This file is a part of the LilBro library 
#
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
# -----------------------------------

from __future__ import division
import time
import odrive
import math
import numpy as np
import globals

#AUTOMATIC  = 1
#MANUAL = 0
#DIRECT = 0
#REVERSE = 1
#P_ON_M = 0
#P_ON_E = 1

class robot():
    """This is the constructor for the robot class.

    In this constructor, the proportional gain, current limit,
    velocity limit, and drivers are initialized and delclared.

    @params self
    @return Unused

    """

    def __init__(self):

        self.pGain = 20
        self.driverCurLim = 50
        self.driverVelLim = 60000
        self.driver1 = 0
        self.driver2 = 0
        self.driver3 = 0
        self.driver4 = 0

        global n, nh, leng_coeff1, leng_coeff2, alpha_coeff1, alpha_coeff2, t

        t = 0.4
        n = 12
        nh = 7
        self.leftShoulderx = np.array([np.zeros(n),np.zeros(n),np.zeros(n),np.zeros(n)])
        self.rightShoulderx = np.array([np.zeros(n),np.zeros(n),np.zeros(n),np.zeros(n)])
        self.leftShouldery = np.array([np.zeros(n),np.zeros(n),np.zeros(n),np.zeros(n)])
        self.rightShouldery = np.array([np.zeros(n),np.zeros(n),np.zeros(n),np.zeros(n)])

        self.leftShoulderxh = np.array([np.zeros(nh),np.zeros(nh),np.zeros(nh),np.zeros(nh)])
        self.rightShoulderxh = np.array([np.zeros(nh),np.zeros(nh),np.zeros(nh),np.zeros(nh)])
        self.leftShoulderyh = np.array([np.zeros(nh),np.zeros(nh),np.zeros(nh),np.zeros(nh)])
        self.rightShoulderyh = np.array([np.zeros(nh),np.zeros(nh),np.zeros(nh),np.zeros(nh)])

        global timeArray
        timeArray = []
        global motorPos, motorVel, motorCur
        motorPos = []
        motorVel = []
        motorCur = []
        global motors0, motors1, motors2, motors3, motors4, motors5, motors6, motors7
        motors0, motors1, motors2, motors3, motors4, motors5, motors6, motors7 = [], [], [], [], [], [], [], []
        global motorsVel0, motorsVel1, motorsVel2, motorsVel3, motorsVel4, motorsVel5, motorsVel6, motorsVel7 
        motorsVel0, motorVel1, motorsVel2, motorsVel3, motorsVel4, motorsVel5, motorsVel6, motorsVel7 = [], [], [], [], [], [], [], []
        global motorsCur0, motorsCur1, motorsCur2, motorsCur3, motorsCur4, motorsCur5, motorsCur6, motorsCur7
        motorsCur0, motorCur1, motorsCur2, motorsCur3, motorsCur4, motorsCur5, motorsCur6, motorsCur7 = [], [], [], [], [], [], [], []

        global theta1_t, theta2_t, theta1_ht, theta2_ht, t1_th, t2_th, theta1f, theta2f, theta1_b, theta2_b

        global ls1_t, ls2_t, as1_t, as2_t, ls1_tBack, ls2_tBack, as1_tBack, as2_tBack, t1_trot, t2_trot, l_down
        l_down = np.linspace(0.135,0.175,nh/4)
        
        t1_trot = np.linspace(0,t/2,n/2)
        t2_trot = np.linspace(t/2,t,n/2)

        t1_th = np.linspace(0,0.4,nh/2)
        t2_th = np.linspace(0.4,0.8,nh)

        theta1f = np.array([np.zeros(n),np.zeros(n),np.zeros(n),np.zeros(n)])
        theta2f = np.array([np.zeros(n),np.zeros(n),np.zeros(n),np.zeros(n)])

        theta1_t = np.array([np.zeros(n),np.zeros(n),np.zeros(n),np.zeros(n)])
        theta2_t = np.array([np.zeros(n),np.zeros(n),np.zeros(n),np.zeros(n)])

        theta1_b = np.array([np.zeros(n),np.zeros(n),np.zeros(n),np.zeros(n)])
        theta2_b = np.array([np.zeros(n),np.zeros(n),np.zeros(n),np.zeros(n)])

        theta1_ht = np.array([np.zeros(nh),np.zeros(nh),np.zeros(nh),np.zeros(nh)])
        theta2_ht = np.array([np.zeros(nh),np.zeros(nh),np.zeros(nh),np.zeros(nh)])
    
    """ findDrivers finds Odrive motor drivers given their serial number in main class

    This method uses the Serial number of an odrive motor driver that is 
    connected via USB. 
    
    @params driverID1,driverID2 
    @return Unused

    """

    def findDrivers(self, driverID1, driverID2, driverID3, driverID4):
        self.driver1 = odrive.find_any("usb",str(driverID1))
        self.driver2 = odrive.find_any("usb",str(driverID2))
        self.driver3 = odrive.find_any("usb",str(driverID3))
        self.driver4 = odrive.find_any("usb",str(driverID4))
        print('Found drivers!')
    
    def getDriver1(self):
        return self.driver1.serial_number
        
    def getDriver2(self):
        return self.driver2.serial_number

    def getDriver3(self):
        return self.driver3.serial_number
        
    def getDriver4(self):
        return self.driver4.serial_number

    def setState(self,xdriver,xstate):
        xdriver.axis0.requested_state = xstate
        xdriver.axis1.requested_state = xstate
    
    def setStates(self,state):
        self.setState(self.driver1,state)
        self.setState(self.driver2,state)
        self.setState(self.driver3,state)
        self.setState(self.driver4,state)

    def setPGain(self,xdriver,xgain):
        xdriver.axis0.controller.config.pos_gain = xgain
        xdriver.axis1.controller.config.pos_gain = xgain

    def setPGains(self,newGain):
        self.setPGain(self.driver1,newGain)
        self.setPGain(self.driver2,newGain)
        self.setPGain(self.driver3,newGain)
        self.setPGain(self.driver4,newGain)

    def setVelGain(self,xdriver,xgain):
        xdriver.axis0.controller.config.vel_gain = xgain
        xdriver.axis1.controller.config.vel_gain = xgain

    def setVelGains(self,newGain):
        self.setVelGain(self.driver1,newGain)
        self.setVelGain(self.driver2,newGain)
        self.setVelGain(self.driver3,newGain)
        self.setVelGain(self.driver4,newGain)

    def setVelIntGain(self,xdriver,xgain):
        xdriver.axis0.controller.config.vel_integrator_gain = xgain
        xdriver.axis1.controller.config.vel_integrator_gain = xgain

    def setVelIntGains(self,newGain):
        self.setVelIntGain(self.driver1,newGain)
        self.setVelIntGain(self.driver2,newGain)
        self.setVelIntGain(self.driver3,newGain)
        self.setVelIntGain(self.driver4,newGain)

    def getPGain(self,axis):
        return axis.controller.config.pos_gain;

    def getVelGain(self):
        return self.driver1.axis0.controller.config.vel_gain;

    def getVelIntGain(self):
        return self.driver1.axis0.controller.config.vel_integrator_gain;

    def addPGain(self,driver,incGain):
        driver.axis0.controller.config.pos_gain += incGain
        driver.axis1.controller.config.pos_gain += incGain

    def addPGains(self,incGain):
        self.addPGain(self.driver1,incGain)
        self.addPGain(self.driver2,incGain)
        self.addPGain(self.driver3,incGain)
        self.addPGain(self.driver4,incGain)
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

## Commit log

2019-02-19 uploaded bipedal walking program
    writing positions from encoder data using WritingPositionFile.py,
    readingStartsequenc.py is the bipedal squatting program for both legs
    updated Squat control
2019-03-29 Added LED class
2019-04-01 Added encoderOffset func
2019-04-06 updated robot class for four drivers

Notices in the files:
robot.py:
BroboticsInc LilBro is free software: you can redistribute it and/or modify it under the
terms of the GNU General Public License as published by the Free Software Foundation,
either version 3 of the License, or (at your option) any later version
